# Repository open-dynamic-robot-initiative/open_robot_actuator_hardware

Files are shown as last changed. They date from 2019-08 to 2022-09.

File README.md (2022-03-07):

# Open Robot Actuator Hardware

**Click on the pictures below for more information**
## Electronics
| TI Evaluation Boards  | BLMC µDriver | Master Board |Details Wiring|
| ---  | --- |--- |---|
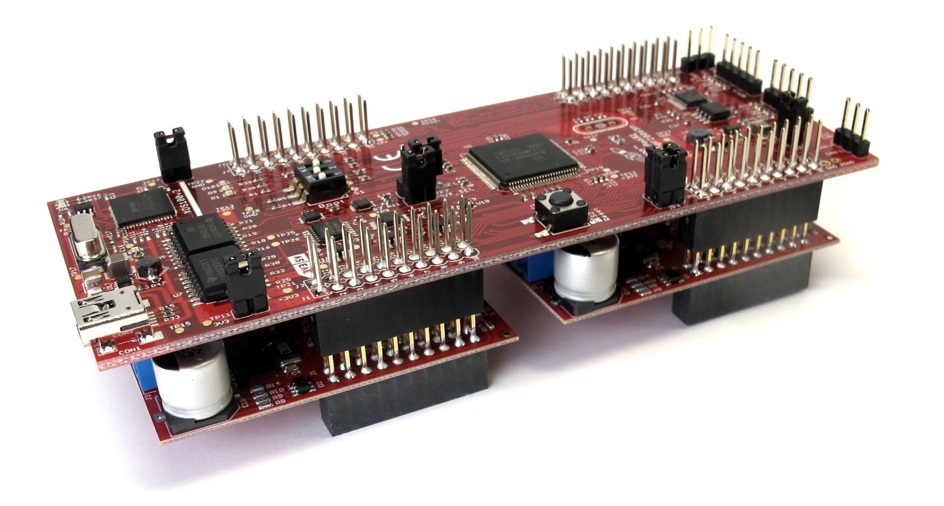
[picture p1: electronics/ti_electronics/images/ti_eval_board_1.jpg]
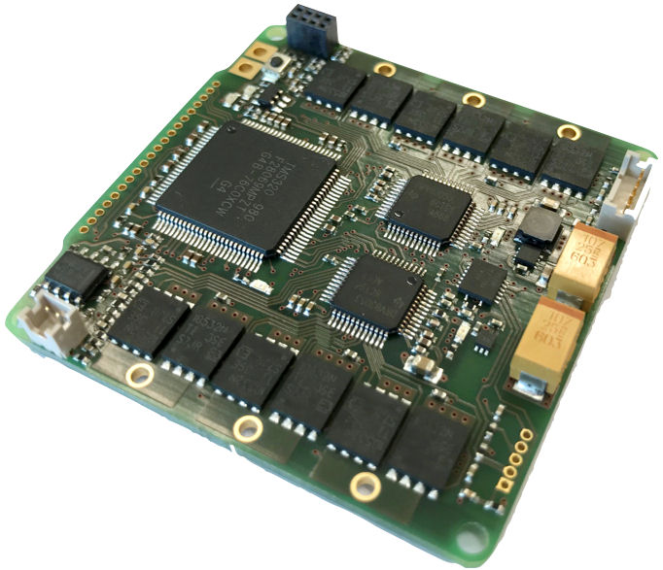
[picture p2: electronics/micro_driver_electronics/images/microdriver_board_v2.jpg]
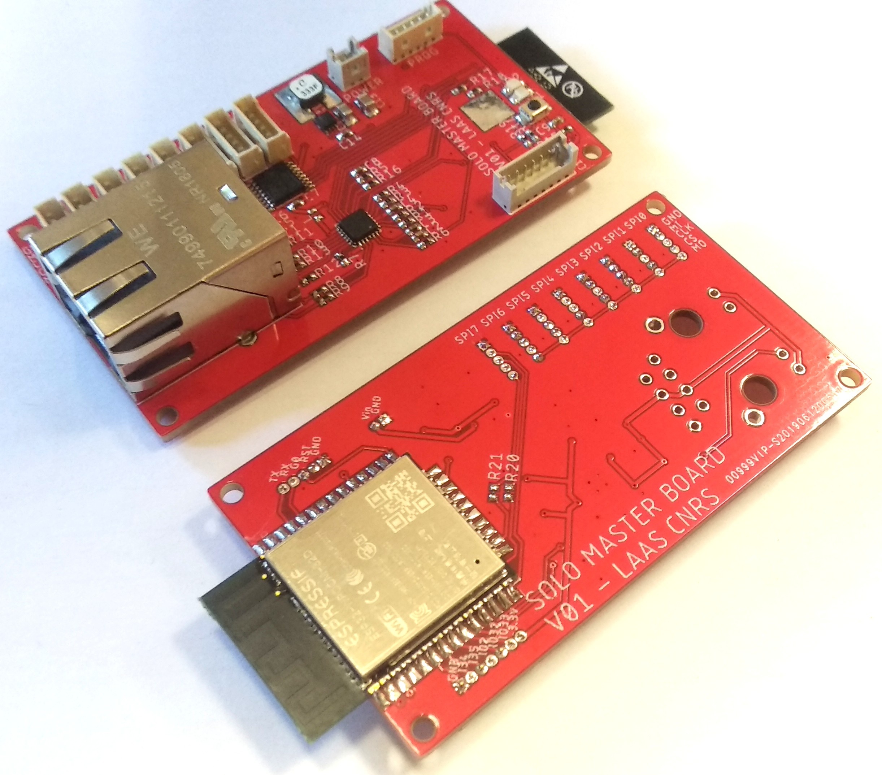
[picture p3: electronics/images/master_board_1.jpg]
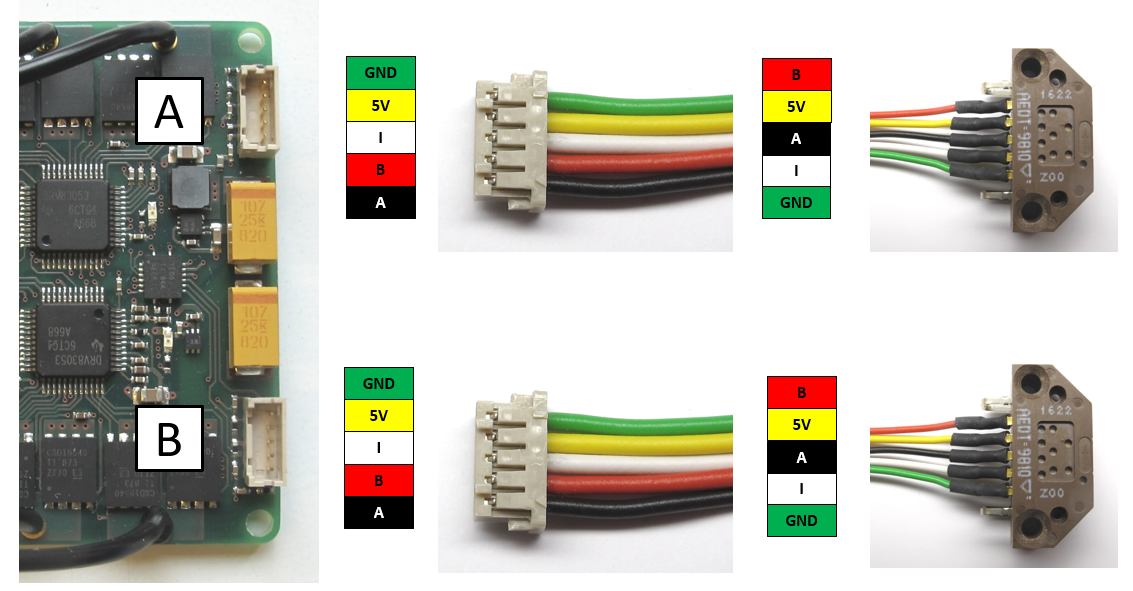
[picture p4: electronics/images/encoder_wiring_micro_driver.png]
| |   |   | |

## Mechanics
| Quadruped 8dof v2 (Solo8) | Quadruped 12dof (Solo12) | Biped 6dof (Bolt) | TriFingerEdu |
| --- | --- |--- |--- |
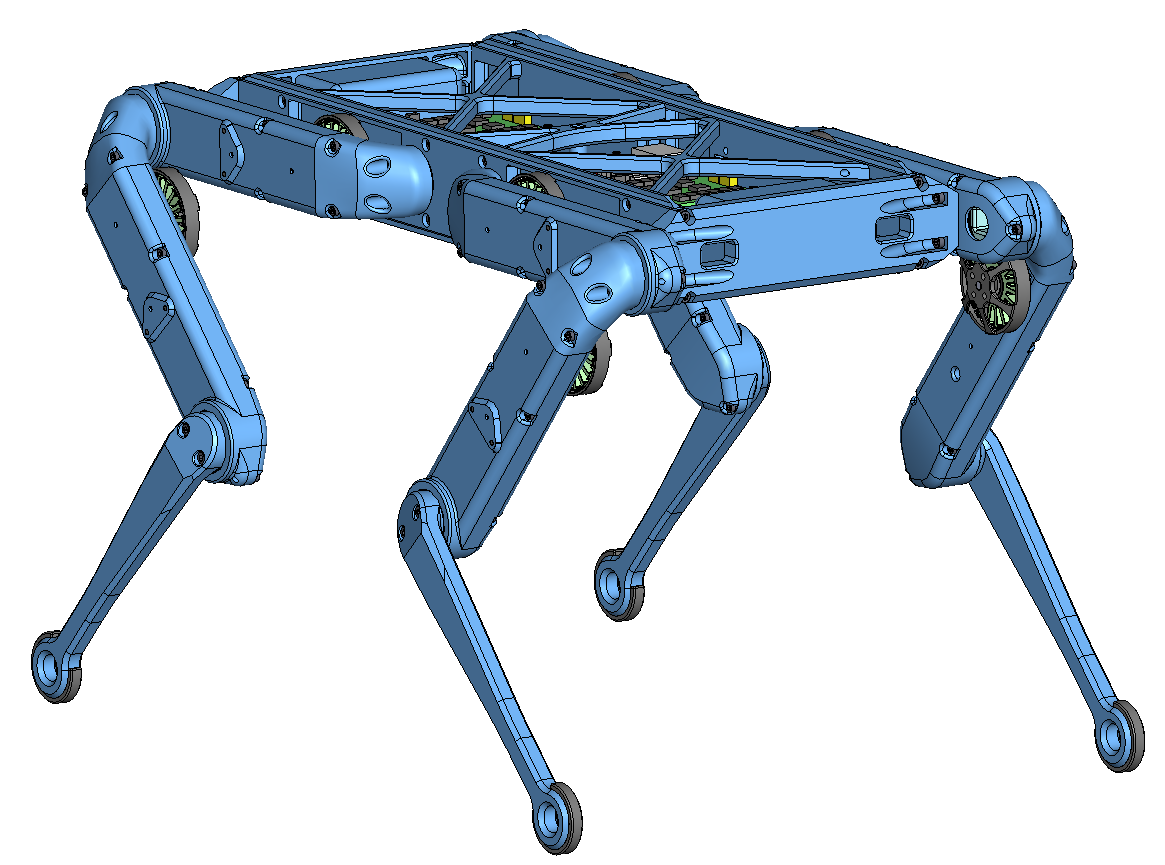
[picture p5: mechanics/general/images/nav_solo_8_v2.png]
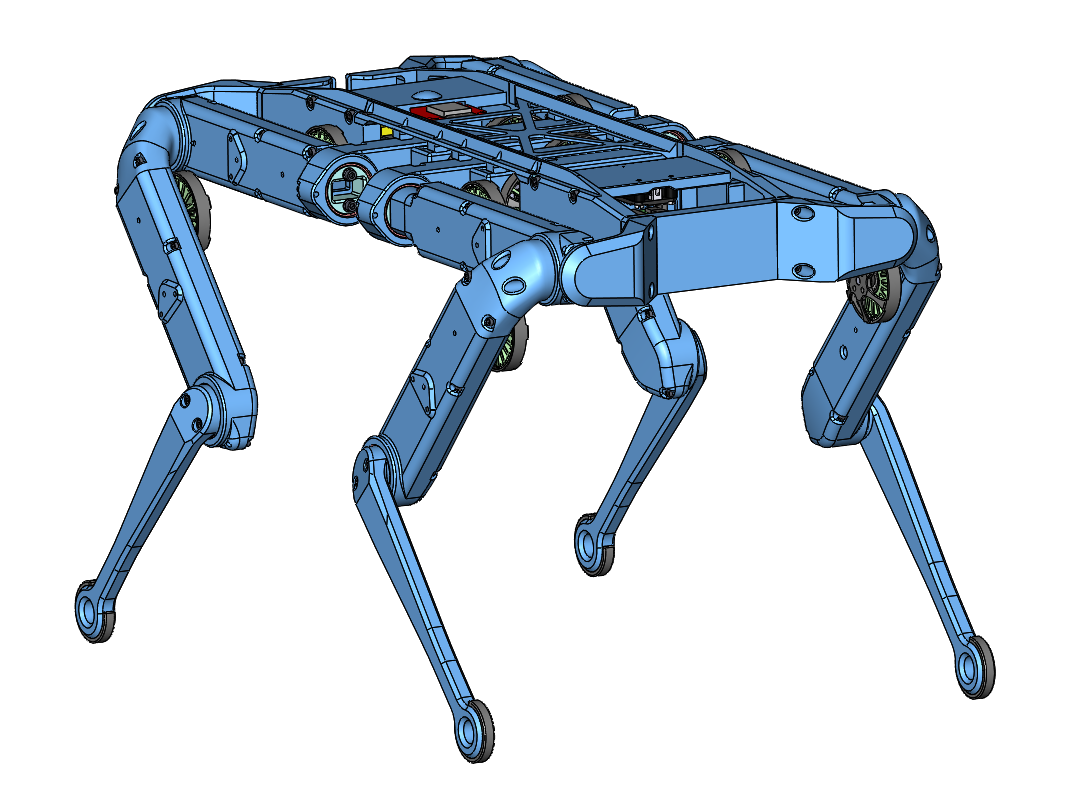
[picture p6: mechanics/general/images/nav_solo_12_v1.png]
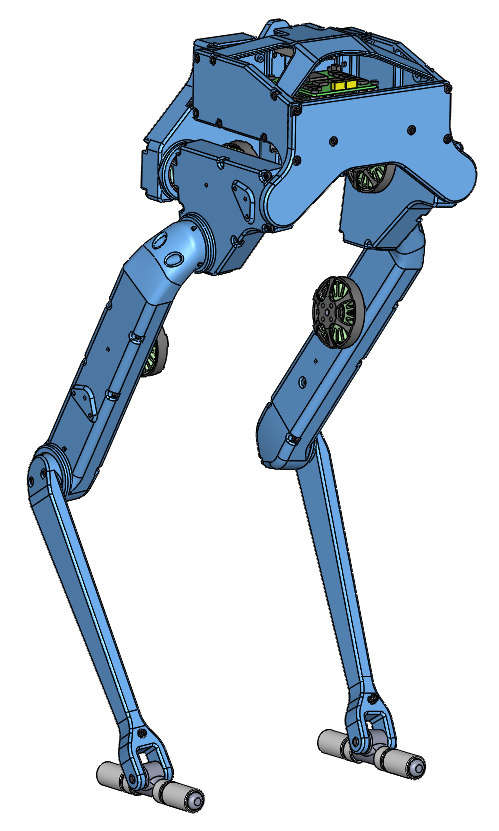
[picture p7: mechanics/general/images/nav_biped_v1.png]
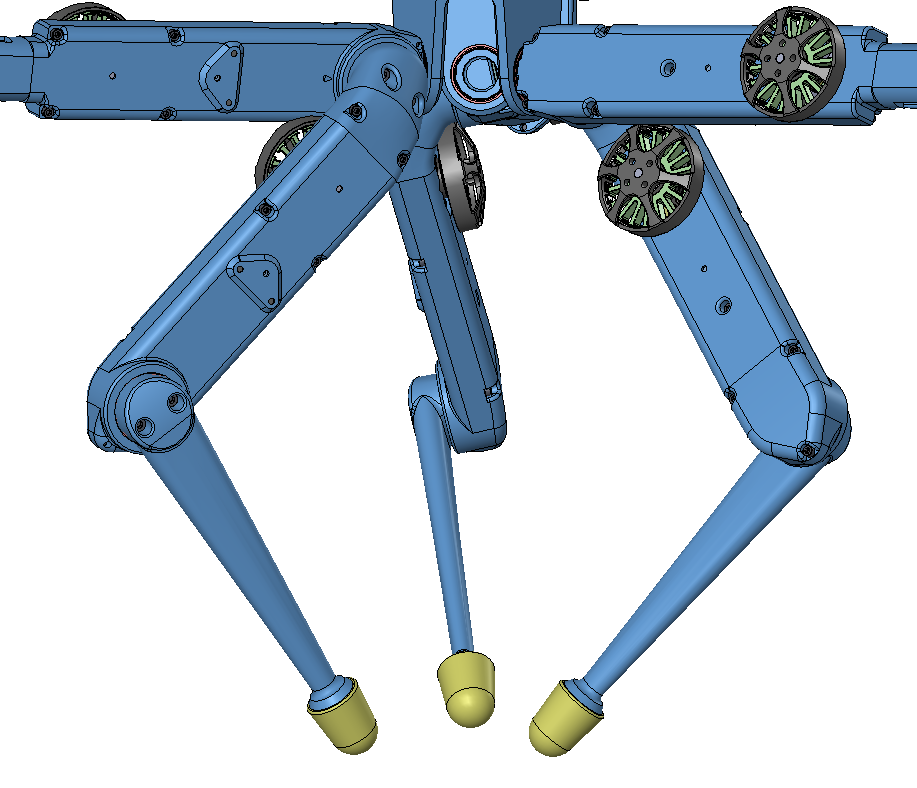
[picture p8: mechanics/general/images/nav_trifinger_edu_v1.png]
|||||

| 2dof Leg v2  | 3dof Leg | Biped Leg |FingerEdu |
| --- | --- |--- |--- |
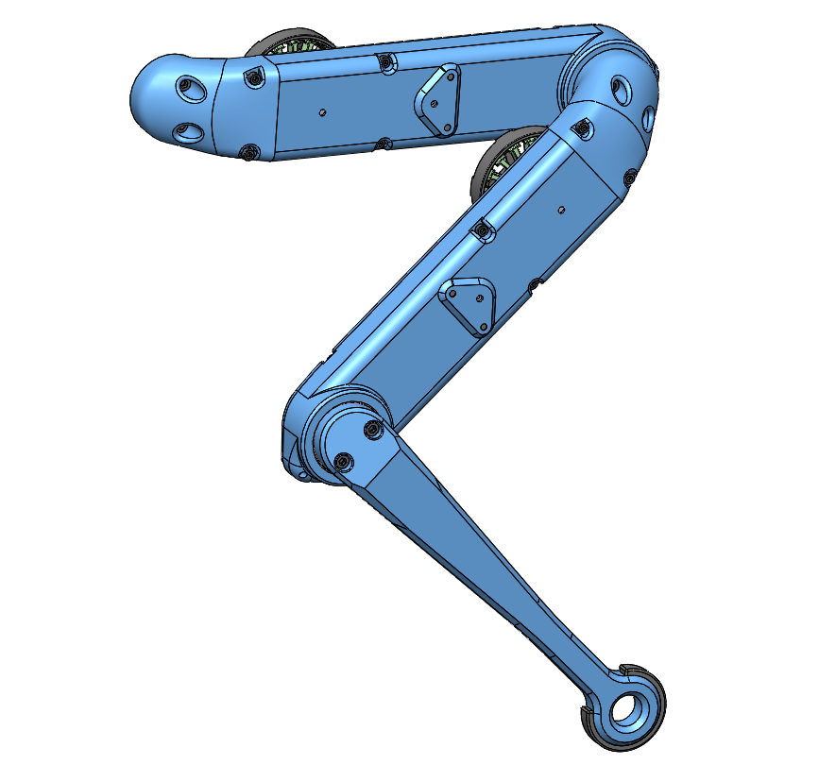
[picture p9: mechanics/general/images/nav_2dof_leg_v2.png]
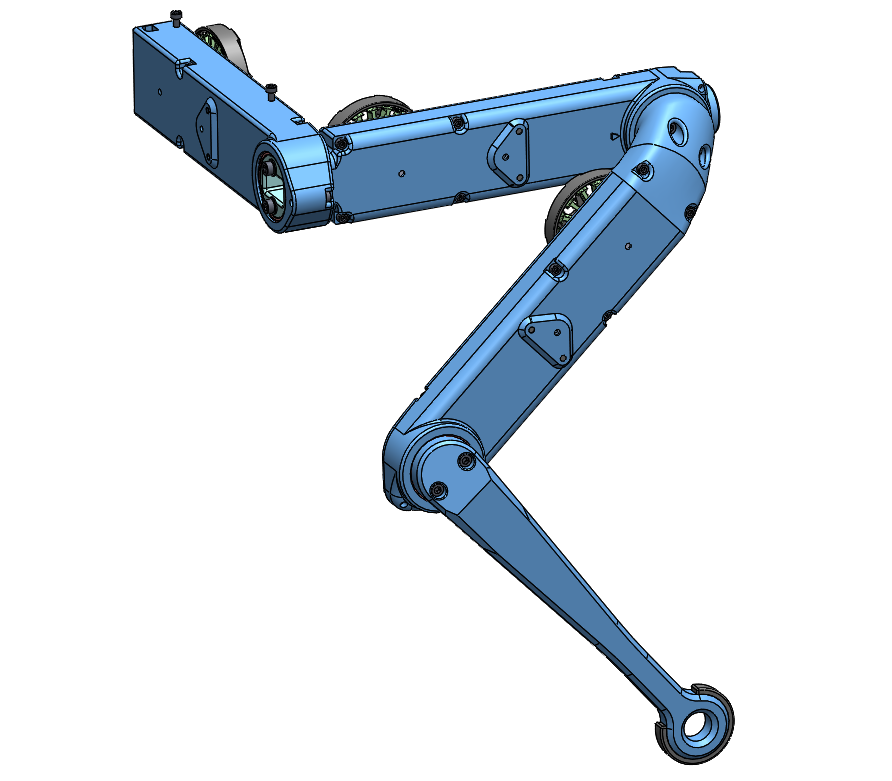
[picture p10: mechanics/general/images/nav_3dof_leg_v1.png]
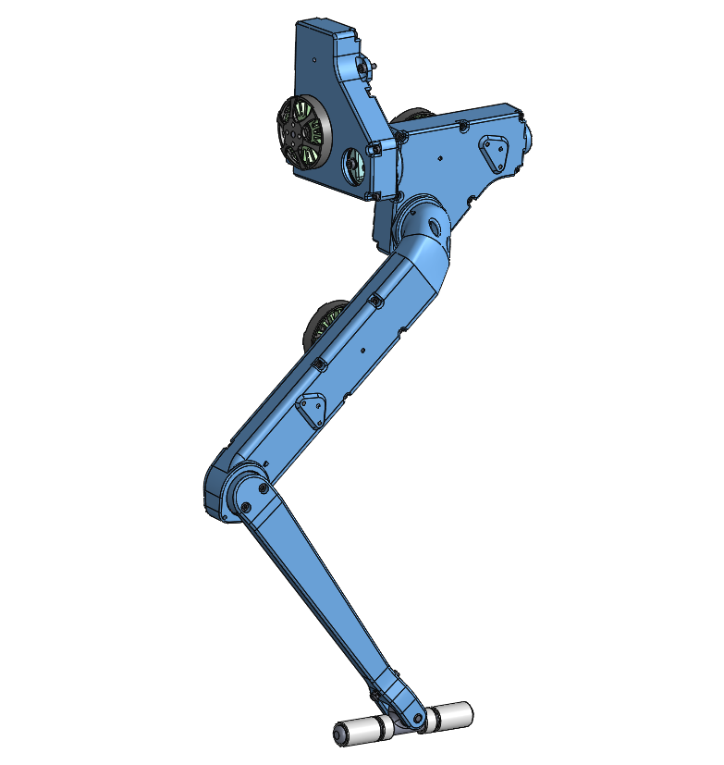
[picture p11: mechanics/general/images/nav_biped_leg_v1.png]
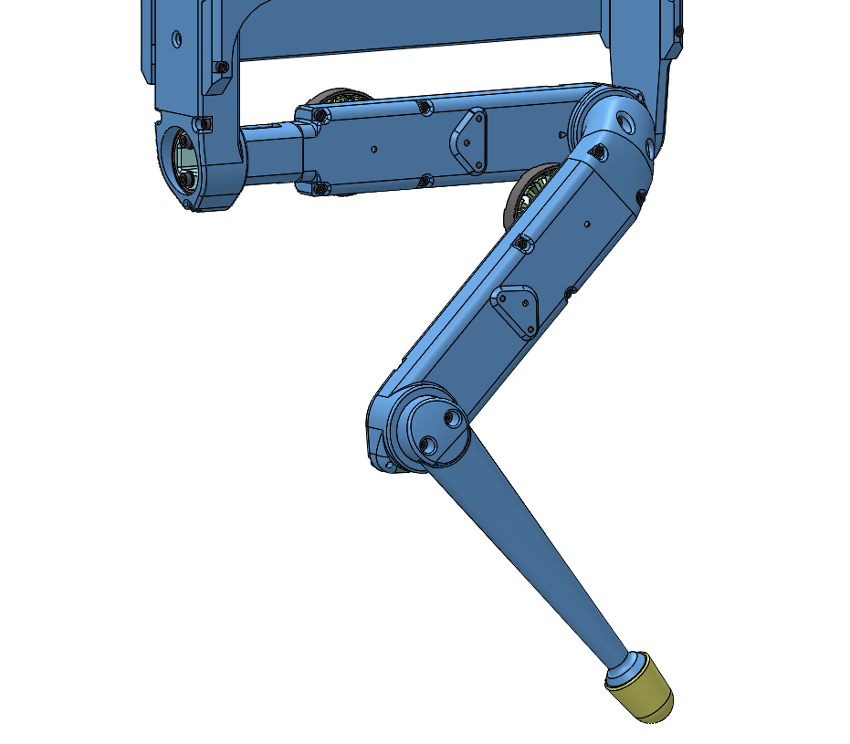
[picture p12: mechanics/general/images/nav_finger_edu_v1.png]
|   |   |   |  |

| Actuator Module Core v1| Actuator Module Core v1.1 | Details 3d Printed Parts | Details Machined Parts |
| ---  | --- |--- |--- |
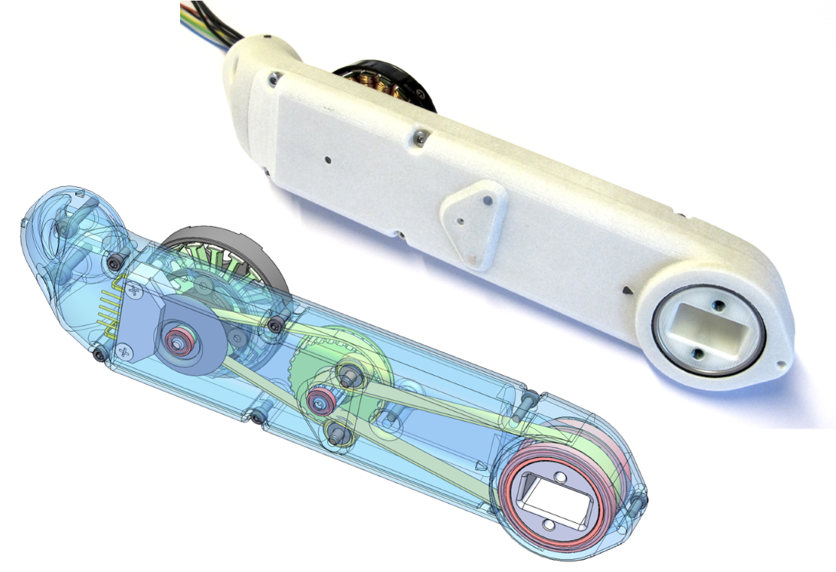
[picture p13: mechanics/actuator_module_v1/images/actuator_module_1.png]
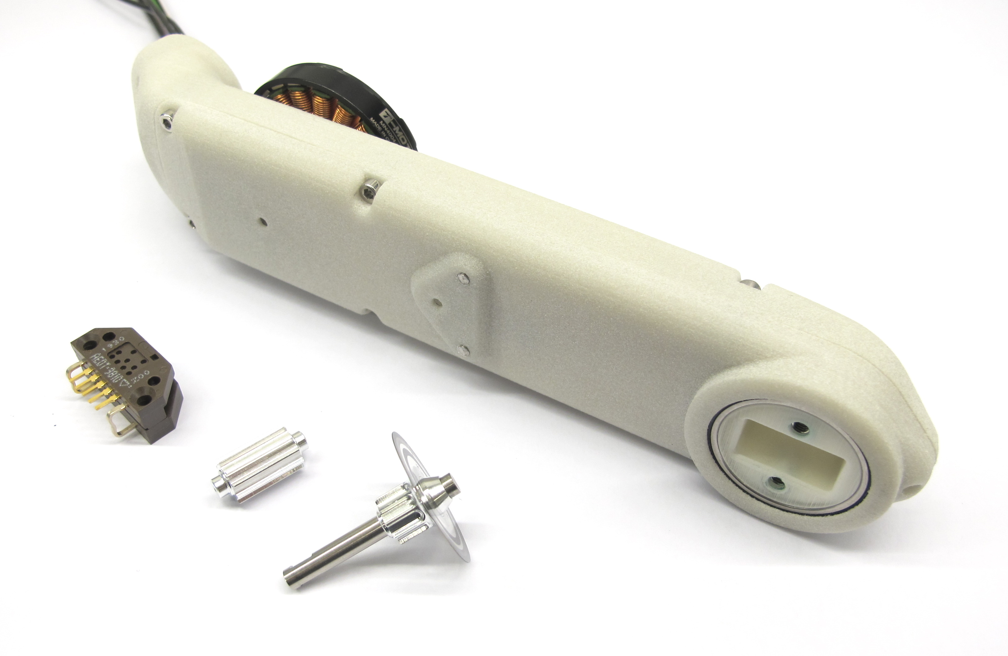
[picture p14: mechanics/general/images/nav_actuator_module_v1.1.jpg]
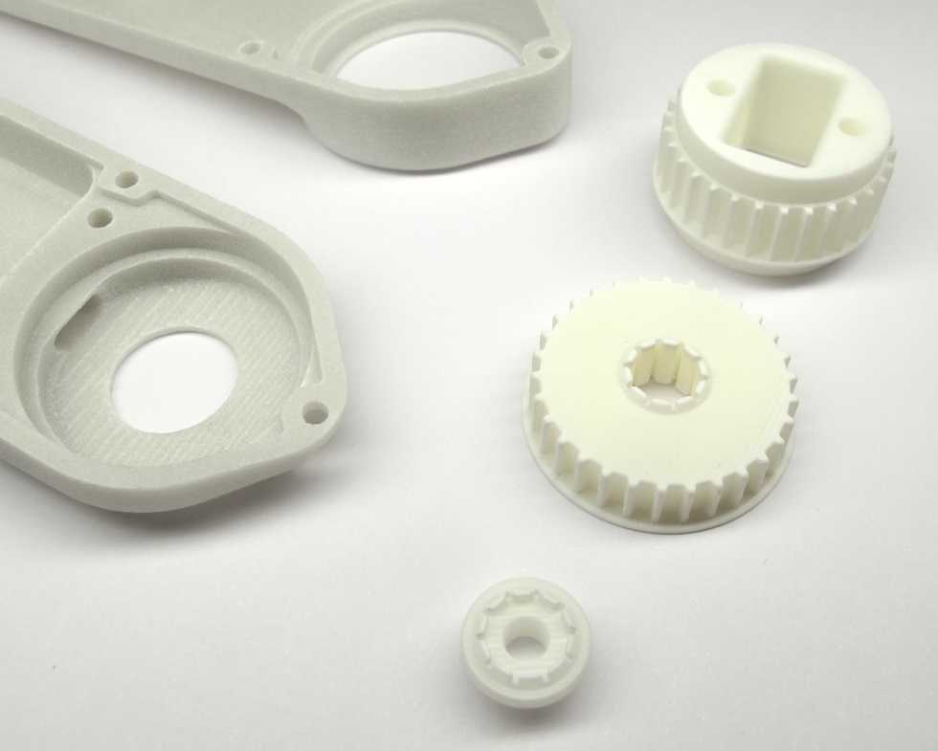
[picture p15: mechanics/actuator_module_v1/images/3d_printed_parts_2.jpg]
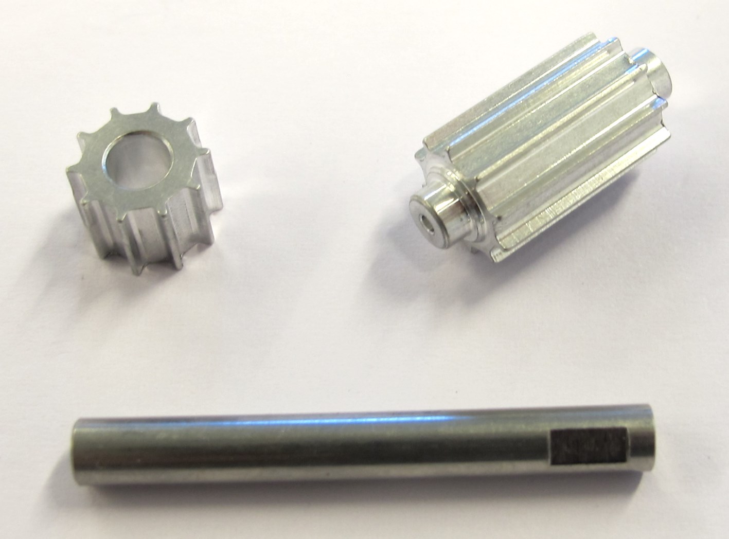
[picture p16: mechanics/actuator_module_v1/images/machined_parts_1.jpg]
| |  | |  |

| Quadruped 12dof v1.1<br>Autonomy Upgrade | Leg Test Stand v2 | NYU Finger | Dual Motor Testbed |
| ---  | --- |--- |---|
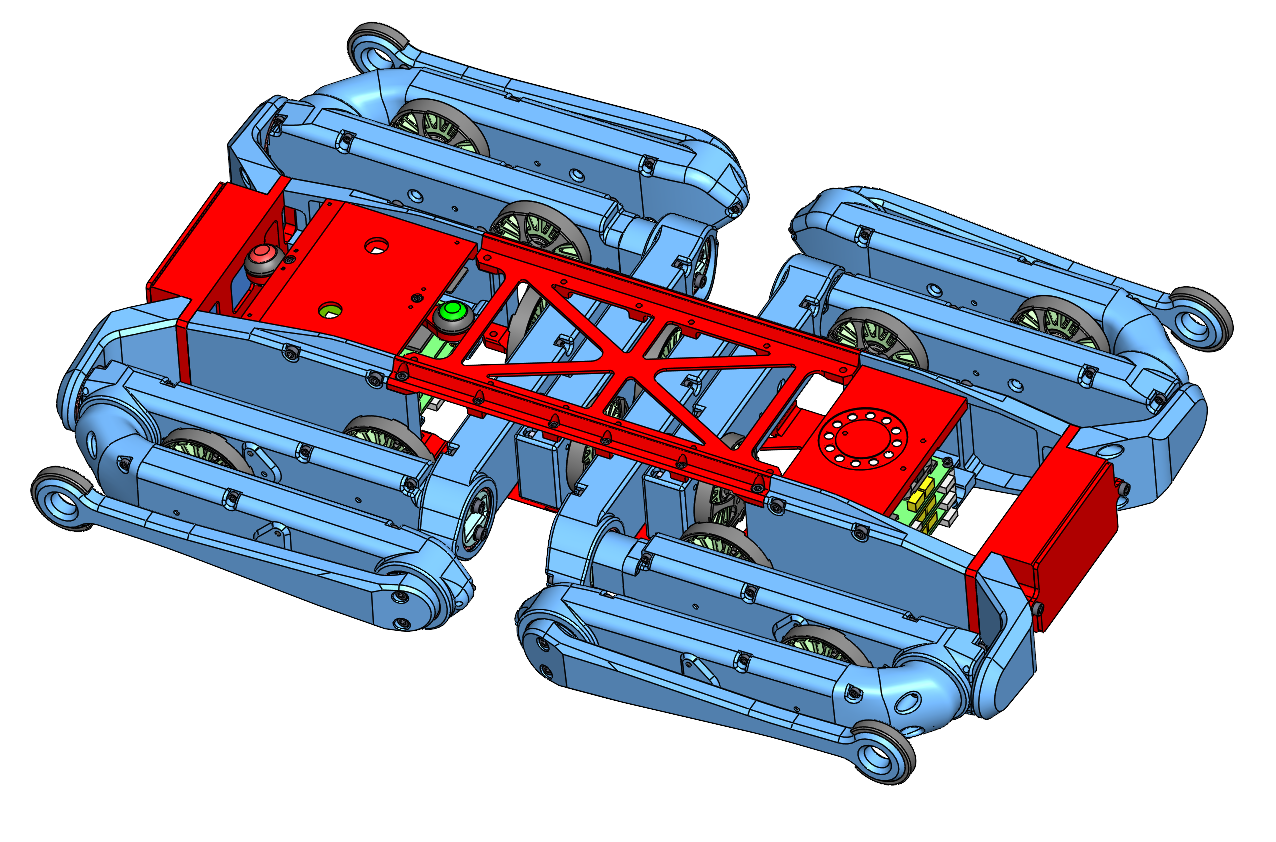
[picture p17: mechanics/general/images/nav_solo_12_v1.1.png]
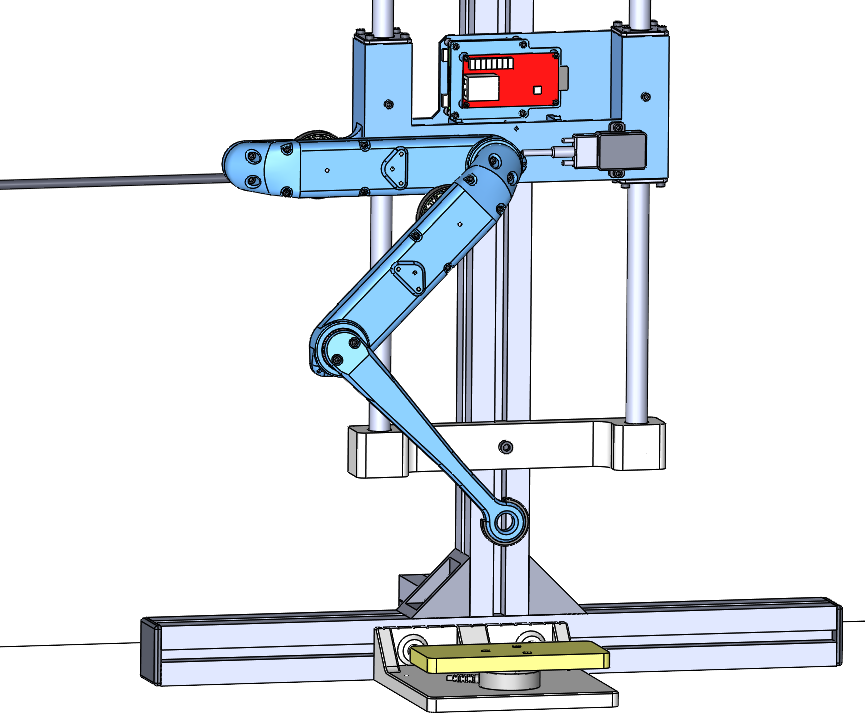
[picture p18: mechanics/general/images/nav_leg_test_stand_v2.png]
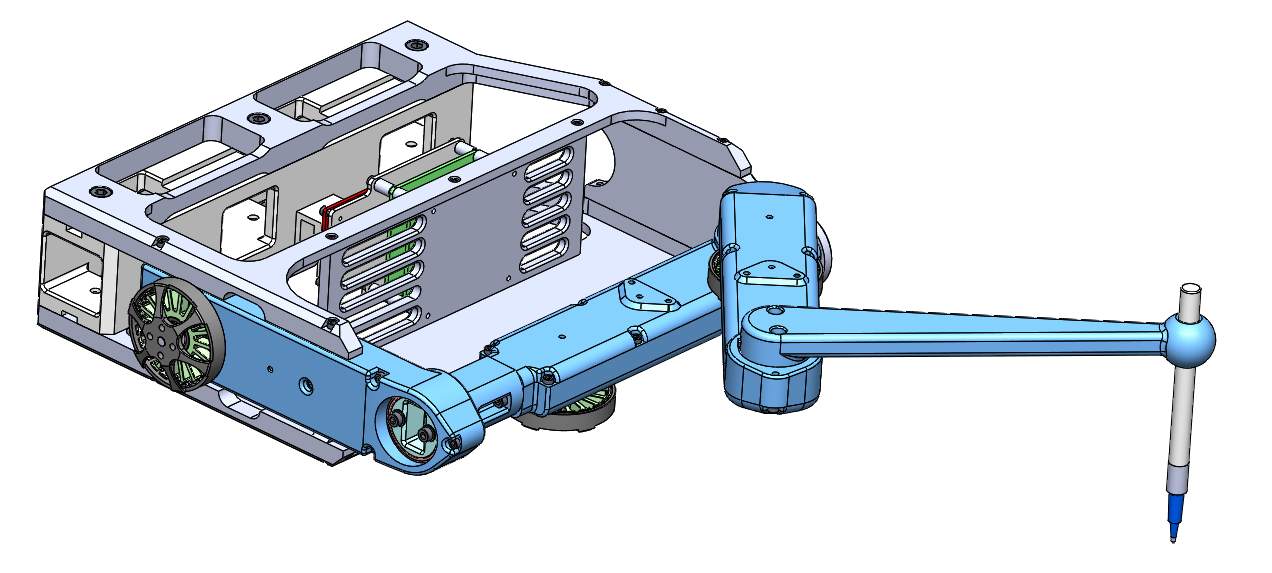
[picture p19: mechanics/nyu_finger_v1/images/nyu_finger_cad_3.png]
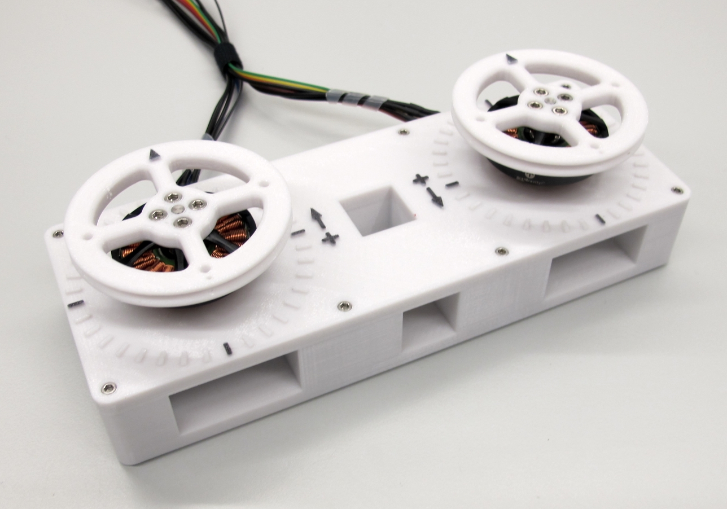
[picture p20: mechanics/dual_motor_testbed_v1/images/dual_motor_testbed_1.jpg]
| |  |  |  |

## More Details
| Mechanical Tools and Consumables |Electronic Components and Tools| Details Electronics<br>Quadruped Robot 12dof | Lower Legs |
| --- | --- | --- |--- |
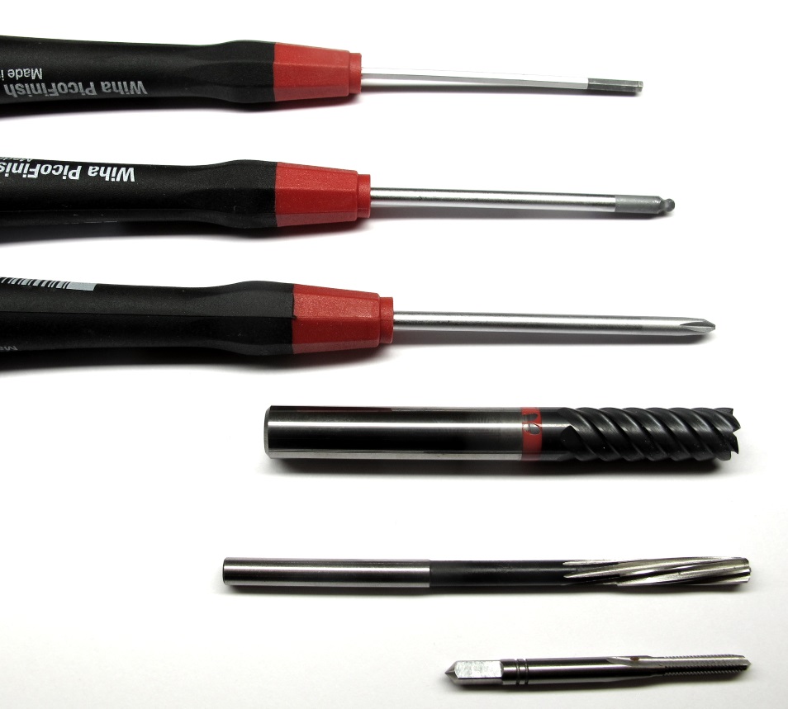
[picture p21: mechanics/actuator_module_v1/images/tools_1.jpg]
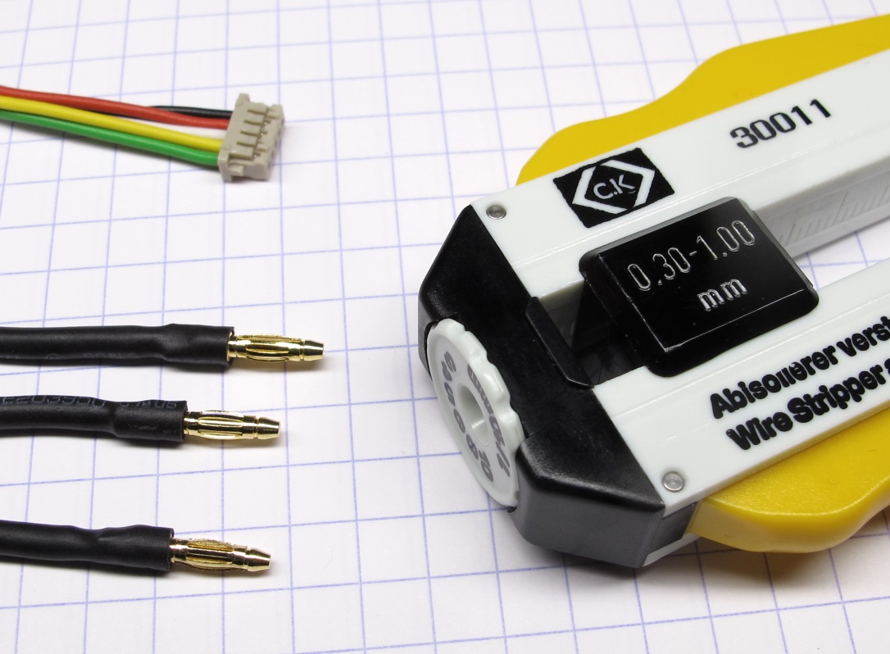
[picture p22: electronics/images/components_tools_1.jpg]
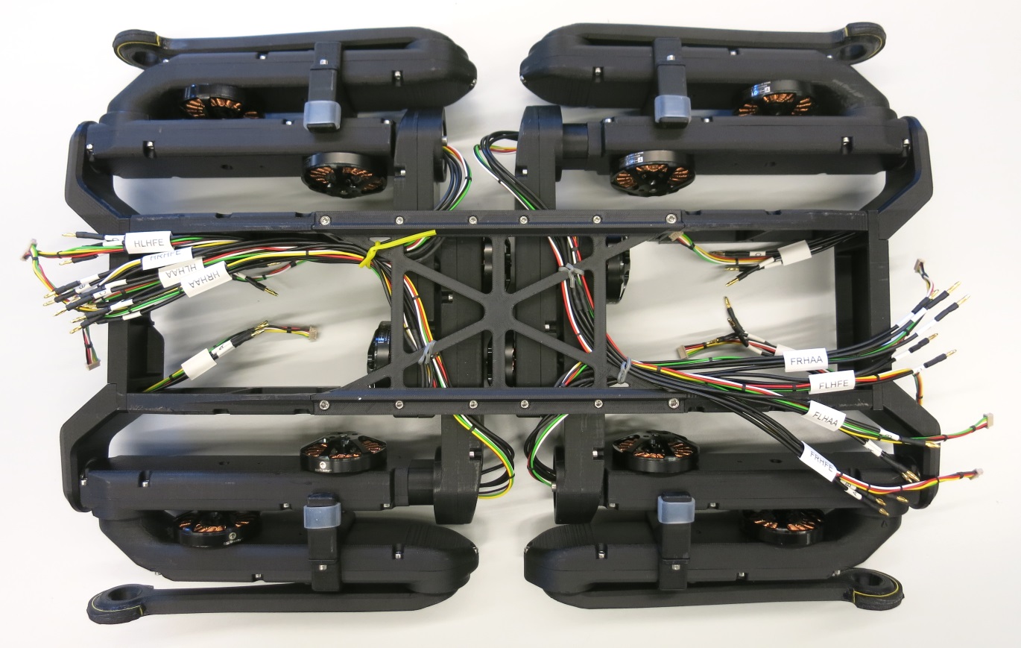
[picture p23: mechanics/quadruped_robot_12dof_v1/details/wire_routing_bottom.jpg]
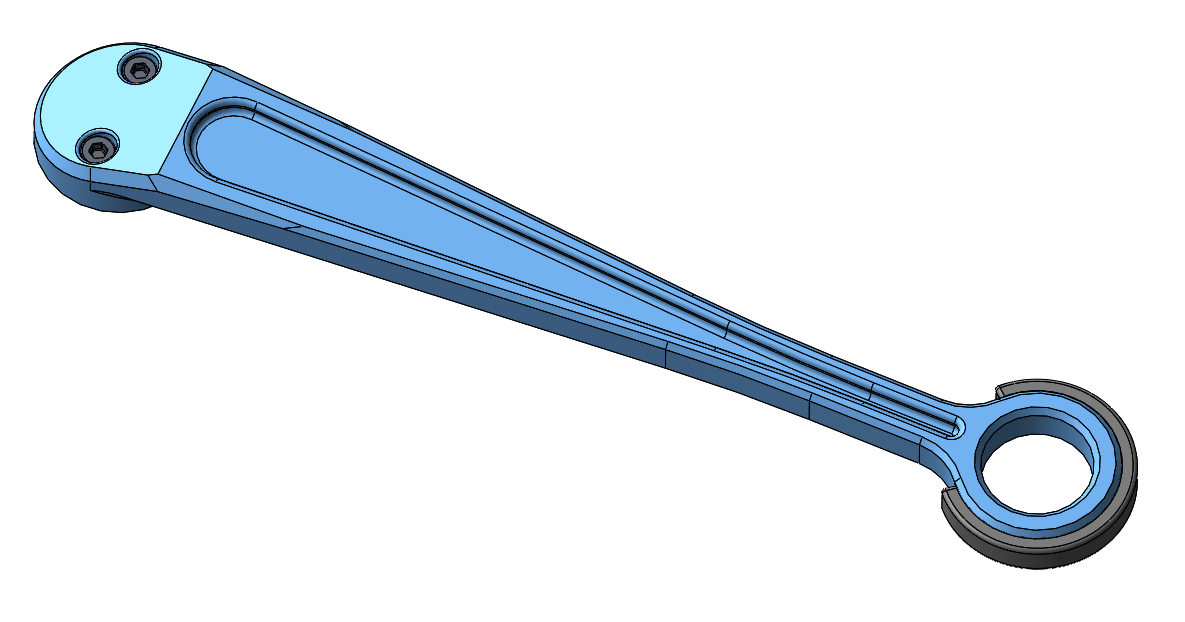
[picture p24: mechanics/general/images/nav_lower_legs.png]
|||  |   |

| Robot Calibration | Conventions | Known Issues |  |
| --- | --- | --- | --- |
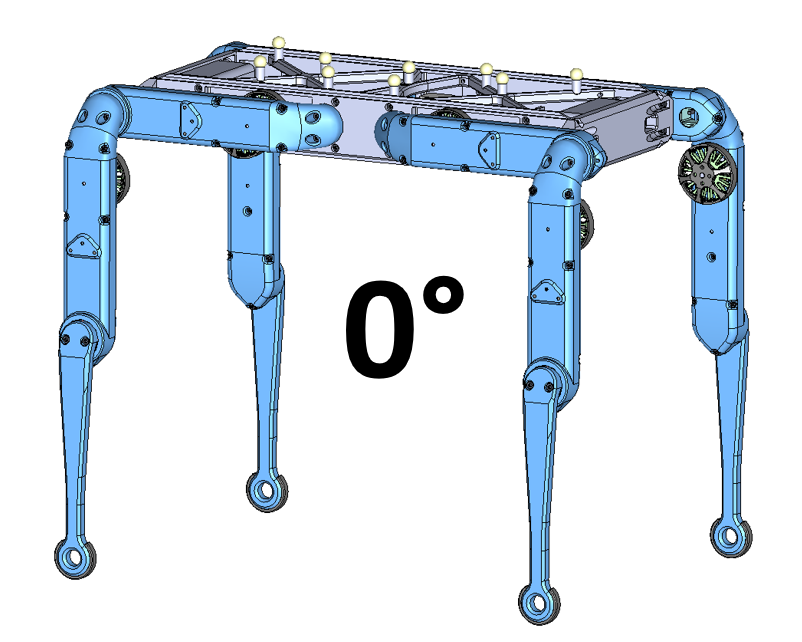
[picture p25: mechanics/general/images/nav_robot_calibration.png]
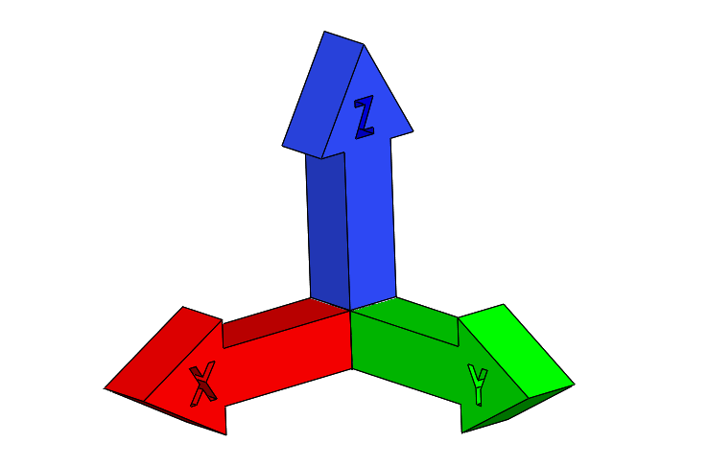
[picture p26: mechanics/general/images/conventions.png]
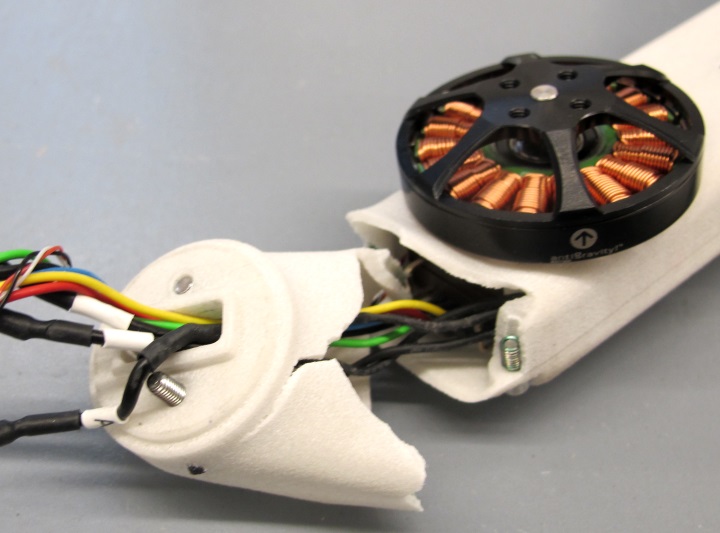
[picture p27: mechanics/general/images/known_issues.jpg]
|||||

## Step-by-Step Instructions
| Motor Preparation  | Motor Shaft Preparation | Encoder Preparation |Center Pulley Preparation|
| --- | --- | --- | --- |
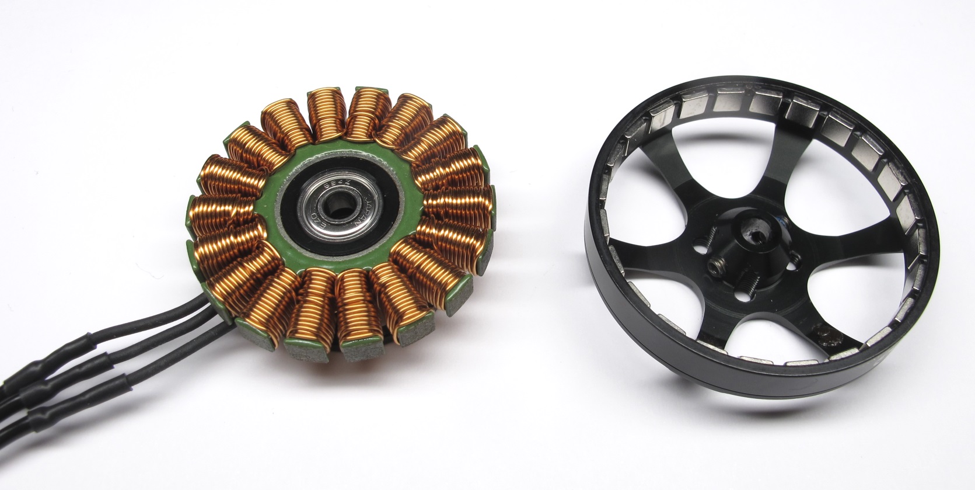
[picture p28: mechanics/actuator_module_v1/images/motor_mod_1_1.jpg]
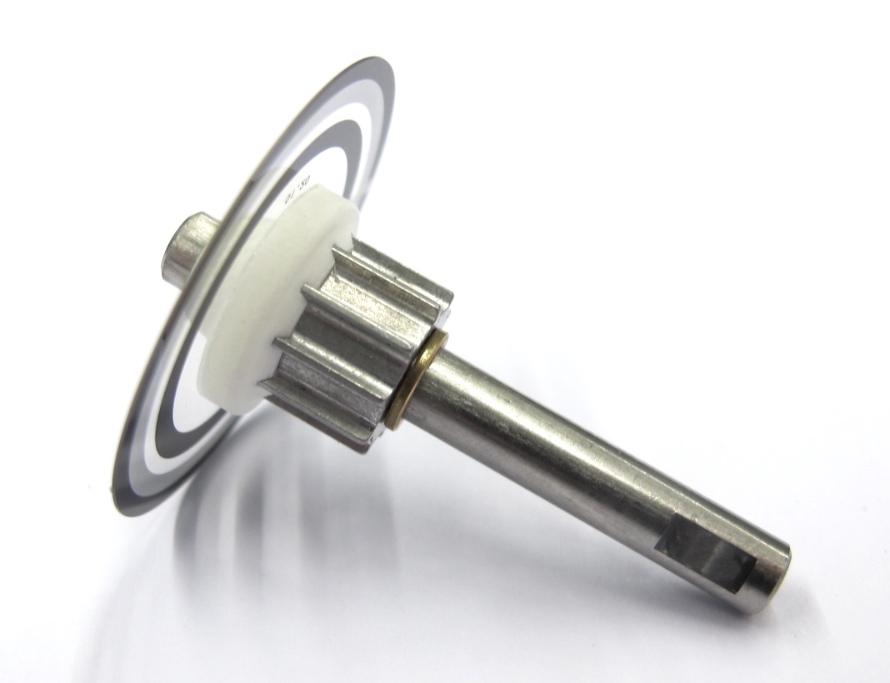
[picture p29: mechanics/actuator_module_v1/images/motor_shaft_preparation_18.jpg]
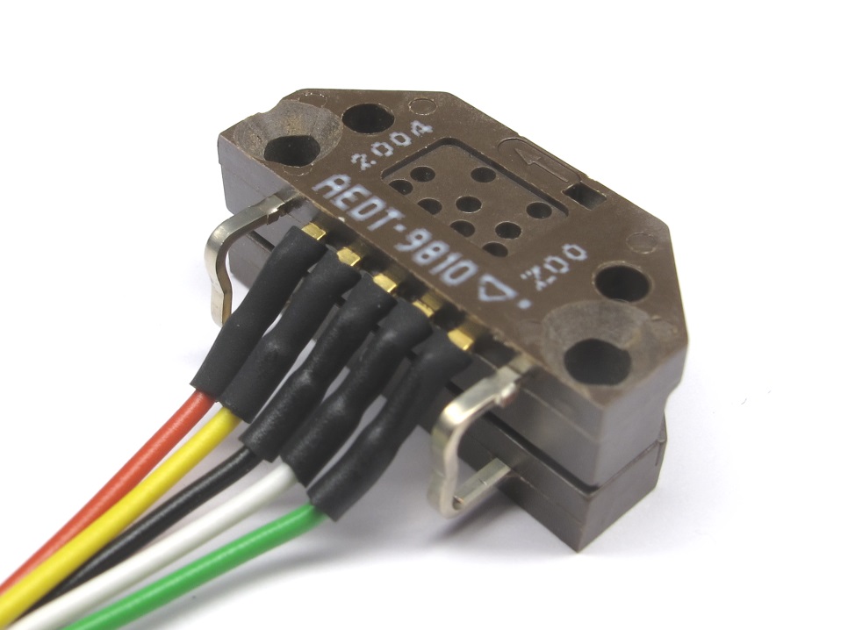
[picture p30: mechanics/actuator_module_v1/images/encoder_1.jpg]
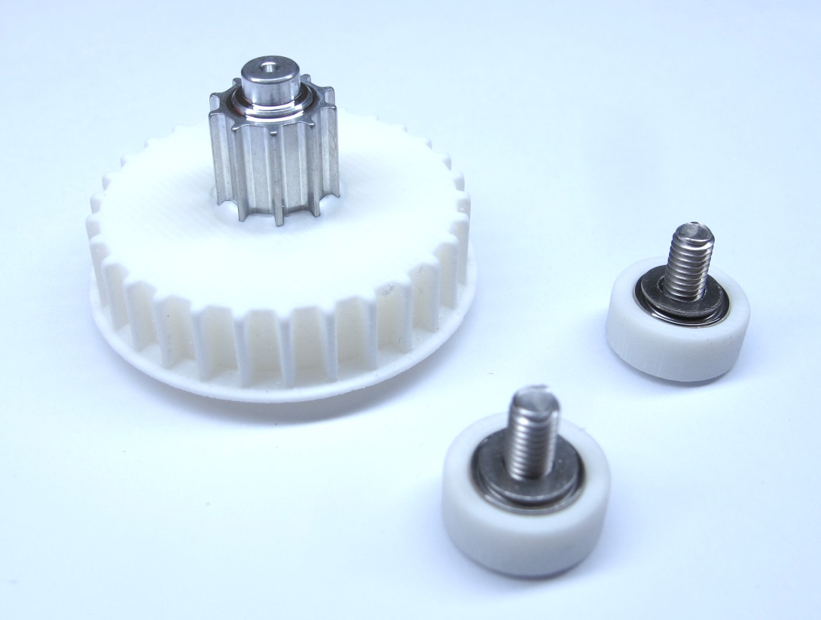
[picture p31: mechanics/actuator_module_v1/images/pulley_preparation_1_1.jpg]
| |   |   | |

| Output Pulley Preparation | Shell Preparation | Actuator Module Assembly |Actuator Module Testing|
| --- | --- | --- | --- |
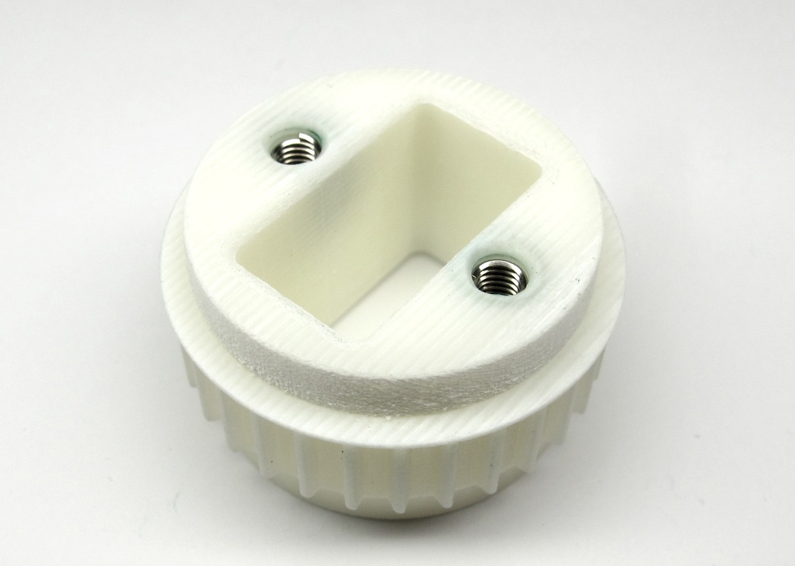
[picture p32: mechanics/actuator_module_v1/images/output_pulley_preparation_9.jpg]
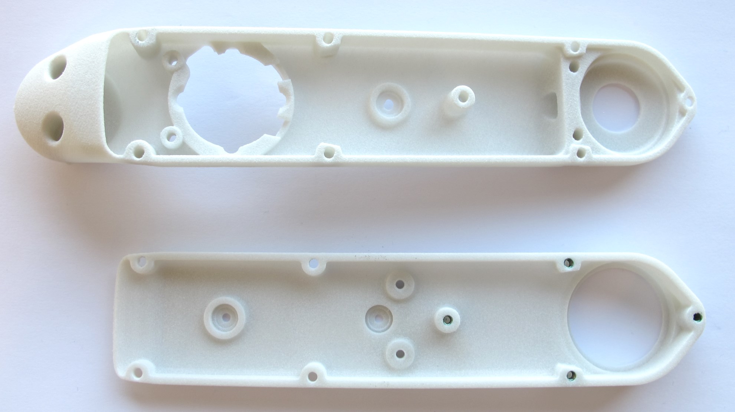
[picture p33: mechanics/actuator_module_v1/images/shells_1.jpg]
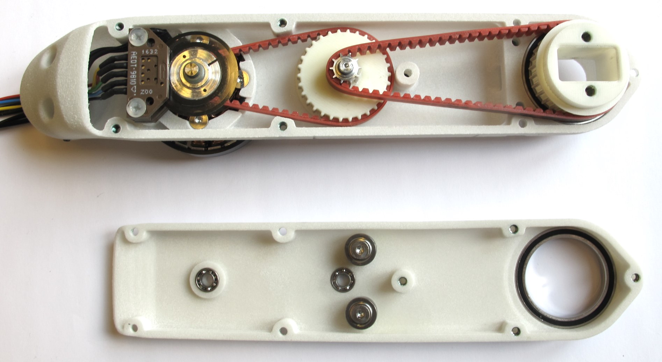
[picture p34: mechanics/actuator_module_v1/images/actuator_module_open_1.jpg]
| |   |   | |

## Old Versions for Reference
| Quadruped 8dof v1 | 2dof Leg v1 | Leg Test Stand v1| Foot Contact Switch |
| ---  | --- |--- |--- |
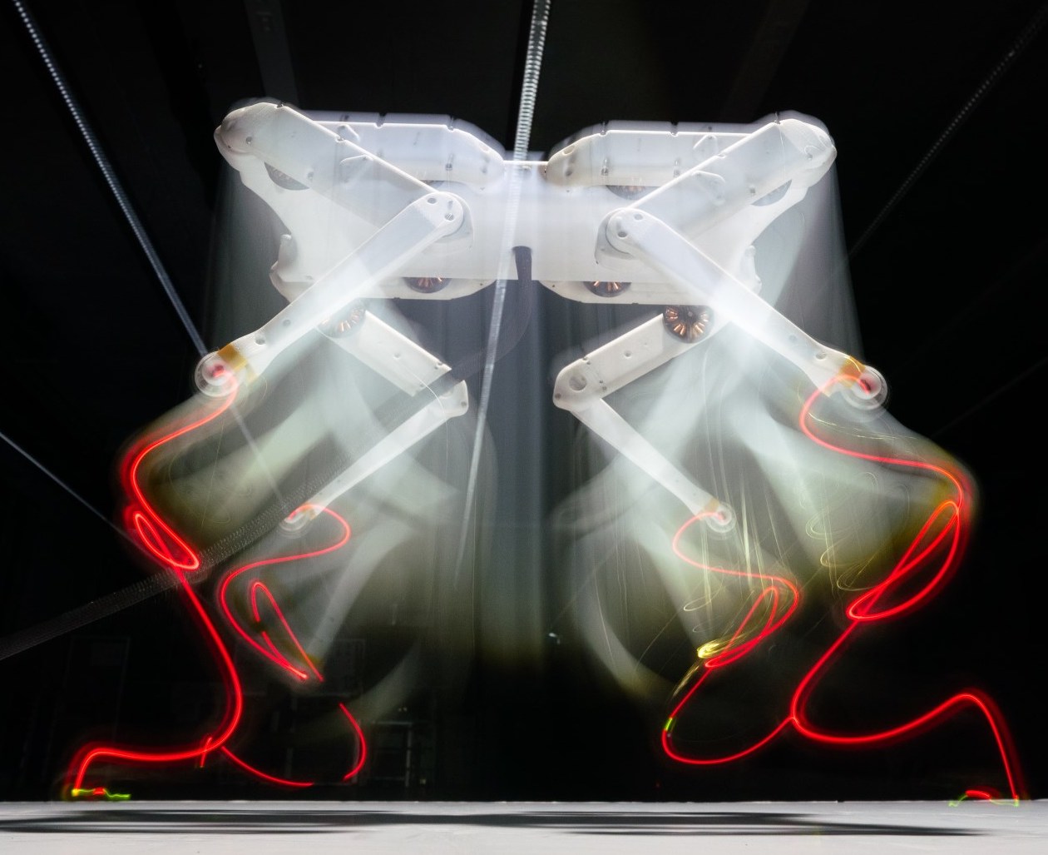
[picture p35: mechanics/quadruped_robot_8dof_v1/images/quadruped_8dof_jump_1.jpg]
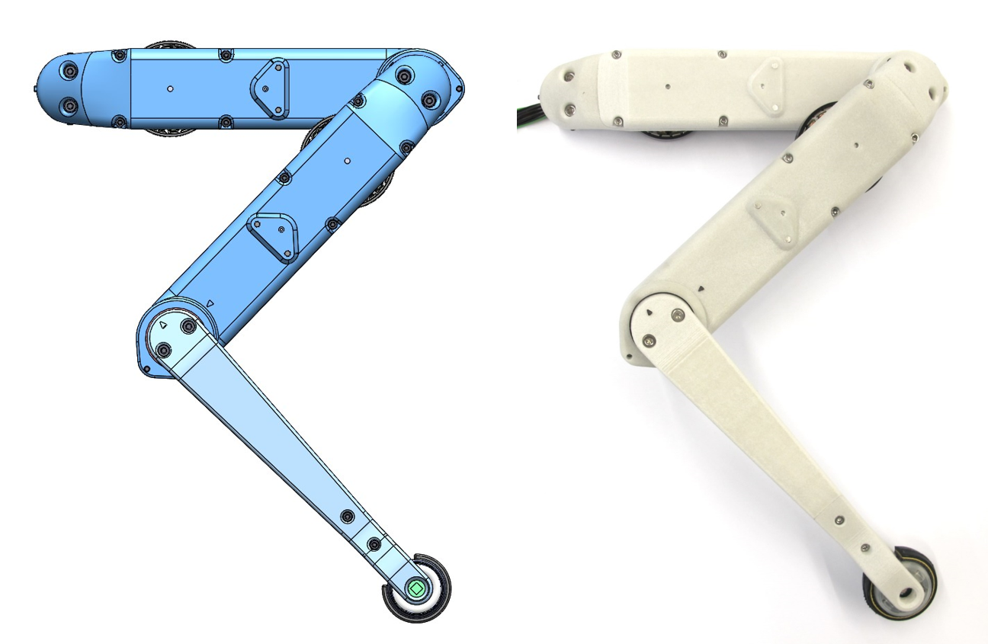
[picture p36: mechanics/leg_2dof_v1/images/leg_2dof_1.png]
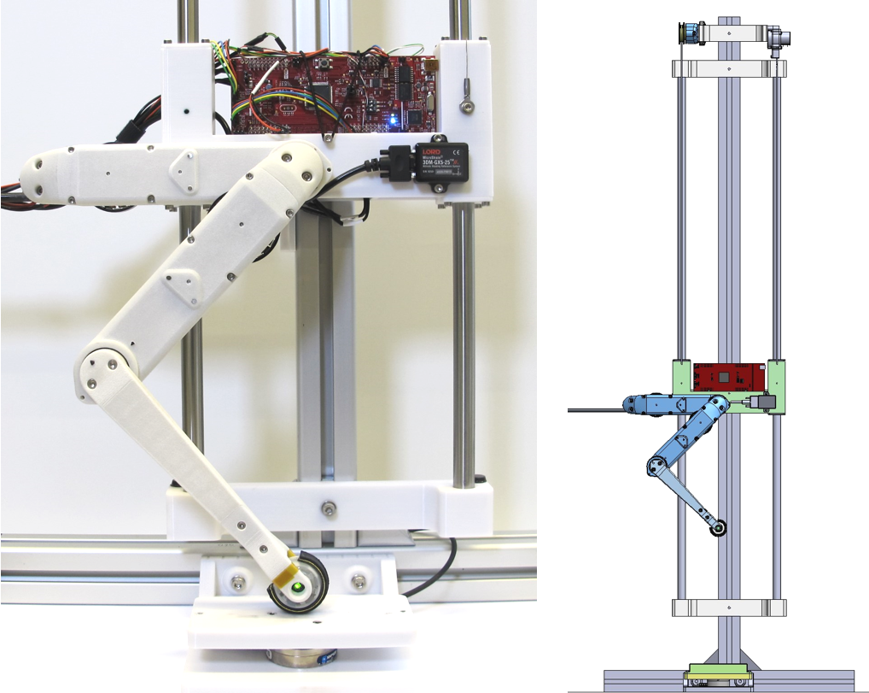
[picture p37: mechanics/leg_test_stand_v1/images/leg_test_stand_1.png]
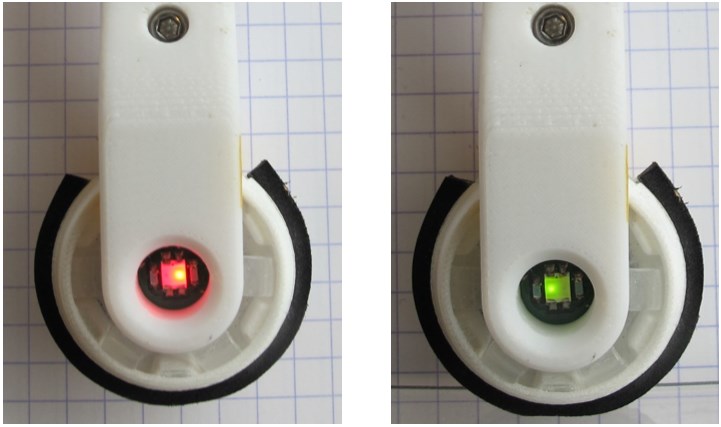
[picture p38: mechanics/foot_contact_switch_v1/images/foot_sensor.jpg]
| | |||

## More Information
[Open Dynamic Robot Initiative - Webpage](https://open-dynamic-robot-initiative.github.io)  
[Open Dynamic Robot Initiative - YouTube Channel](https://www.youtube.com/channel/UCx32JW2oIrax47Gjq8zNI-w)   
[Open Dynamic Robot Initiative - Forum](https://odri.discourse.group/categories)  
[Open Dynamic Robot Initiative - Paper](https://arxiv.org/pdf/1910.00093.pdf)  
[Hardware Overview](#open-robot-actuator-hardware)  
[Software Overview](https://github.com/open-dynamic-robot-initiative/open-dynamic-robot-initiative.github.io/wiki)  

## Authors
Jonathan Fiene  
Thomas Flayols  
Felix Grimminger  

## License
BSD 3-Clause License

## Copyright
Copyright (c) 2019-2021, Max Planck Gesellschaft and New York University

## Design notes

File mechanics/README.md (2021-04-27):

# Open Robot Actuator Mechanics

**Click on the pictures below for more information**

| Quadruped 8dof v2 | Quadruped 12dof | Biped 6dof | TriFingerEdu |
| ---  | --- |--- |--- |
|||||

| 2dof Leg v2  | 3dof Leg | Biped Leg |FingerEdu |
| --- | --- |--- |--- |
|   |   |   |  |

| Actuator Module Core v1| Actuator Module Core v1.1 | Details 3d Printed Parts | Details Machined Parts |
| ---  | --- |--- |--- |
| |  | |  |

| Quadruped 12dof v1.1<br>Autonomy Upgrade | Leg Test Stand v2 | NYU Finger | Dual Motor Testbed |
| ---  | --- |--- |---|
| |  |  |  |

## More Details
| Mechanical Tools and Consumables |Electronic Components and Tools| Details Electronics<br>Quadruped Robot 12dof | Lower Legs |
| --- | --- | --- |--- |
|||  |   |

| Robot Calibration | Conventions | Known Issues |  |
| --- | --- | --- | --- |
|||||

## Step-by-Step Instructions
| Motor Preparation  | Motor Shaft Preparation | Encoder Preparation |Center Pulley Preparation|
| --- | --- | --- | --- |
| |   |   | |

| Output Pulley Preparation | Shell Preparation | Actuator Module Assembly |Actuator Module Testing|
| --- | --- | --- | --- |
| |   |   | |

## Old Versions for Reference
| Quadruped 8dof v1 | 2dof Leg v1 | Leg Test Stand v1| Foot Contact Switch |
| ---  | --- |--- |--- |
| | |||

## More Information
[Open Dynamic Robot Initiative - Webpage](https://open-dynamic-robot-initiative.github.io)  
[Open Dynamic Robot Initiative - YouTube Channel](https://www.youtube.com/channel/UCx32JW2oIrax47Gjq8zNI-w)   
[Open Dynamic Robot Initiative - Forum](https://odri.discourse.group/categories)  
[Open Dynamic Robot Initiative - Paper](https://arxiv.org/pdf/1910.00093.pdf)  
[Hardware Overview](../README.md#open-robot-actuator-hardware)  
[Software Overview](https://github.com/open-dynamic-robot-initiative/open-dynamic-robot-initiative.github.io/wiki)  

## Authors
Jonathan Fiene  
Thomas Flayols  
Felix Grimminger  

## License
BSD 3-Clause License

## Copyright
Copyright (c) 2019-2021, Max Planck Gesellschaft and New York University

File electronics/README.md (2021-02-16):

# Open Robot Actuator Electronics

<br>**Click on the pictures below for more information**
## Electronics
| TI Evaluation Boards  | BLMC µDriver | Master Board |Details Wiring|
| ---  | --- |--- |---|
| |   |   | |

---
## More Information
[Open Dynamic Robot Initiative - Webpage](https://open-dynamic-robot-initiative.github.io)  
[Open Dynamic Robot Initiative - YouTube Channel](https://www.youtube.com/channel/UCx32JW2oIrax47Gjq8zNI-w)   
[Open Dynamic Robot Initiative - Forum](https://odri.discourse.group/categories)  
[Open Dynamic Robot Initiative - Paper](https://arxiv.org/pdf/1910.00093.pdf)  
[Hardware Overview](../#open-robot-actuator-hardware)  
[Software Overview](https://github.com/open-dynamic-robot-initiative/open-dynamic-robot-initiative.github.io/wiki)  

---
## Authors
Jonathan Fiene  
Thomas Flayols  
Felix Grimminger  

## License
BSD 3-Clause License

## Copyright
Copyright (c) 2019-2021, Max Planck Gesellschaft and New York University

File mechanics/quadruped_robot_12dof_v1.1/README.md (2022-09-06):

# Quadruped Robot 12dof v1.1
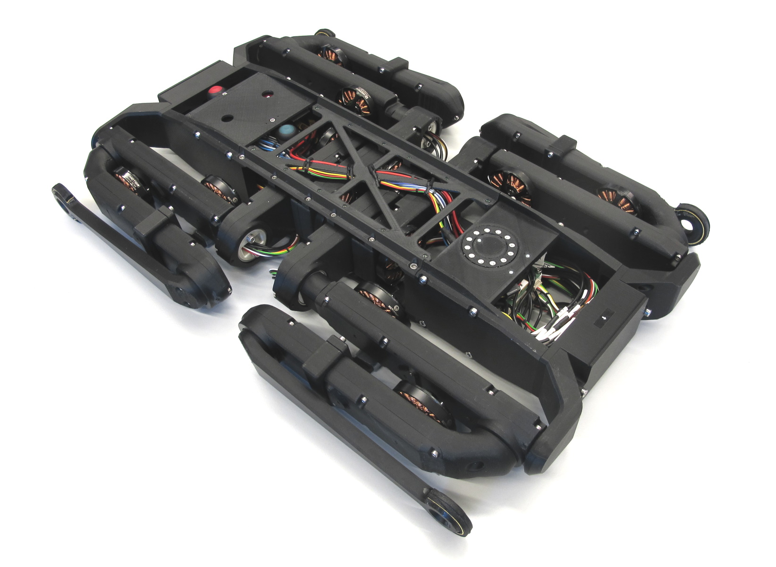
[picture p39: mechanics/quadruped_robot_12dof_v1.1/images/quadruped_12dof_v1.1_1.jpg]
<br>*Quadruped Robot 12dof v1.1 - Autonomy Upgrade - Weight: 2,8kg*<br>

## Description

* this page describes the autonomy upgrade for the [Quadruped 12dof v1 Robot](../quadruped_robot_12dof_v1/README.md#quadruped-robot-12dof-v1)
* onboard batteries and wireless communication will enable the robot to operate without power and ethernet wires
* using the onboard imu for state estimation will enable the robot to operate outside of the motion capture area
* the robot will carry two lithium polymer batteries - one battery pack in the front and one battery pack in the back of the robot
* the custom power management board will enable safe operation of the batteries, e-stop handling and real-time current and battery voltage measurements
* there is a status led ring with 12 RGB leds on the top of the robot
* there are two payload interfaces with mounting holes to attach additional components to the top or the bottom of the robot
* the estimated weight increase for this upgrade is about 300g
* the components that were upgraded are marked red in the screenshot below

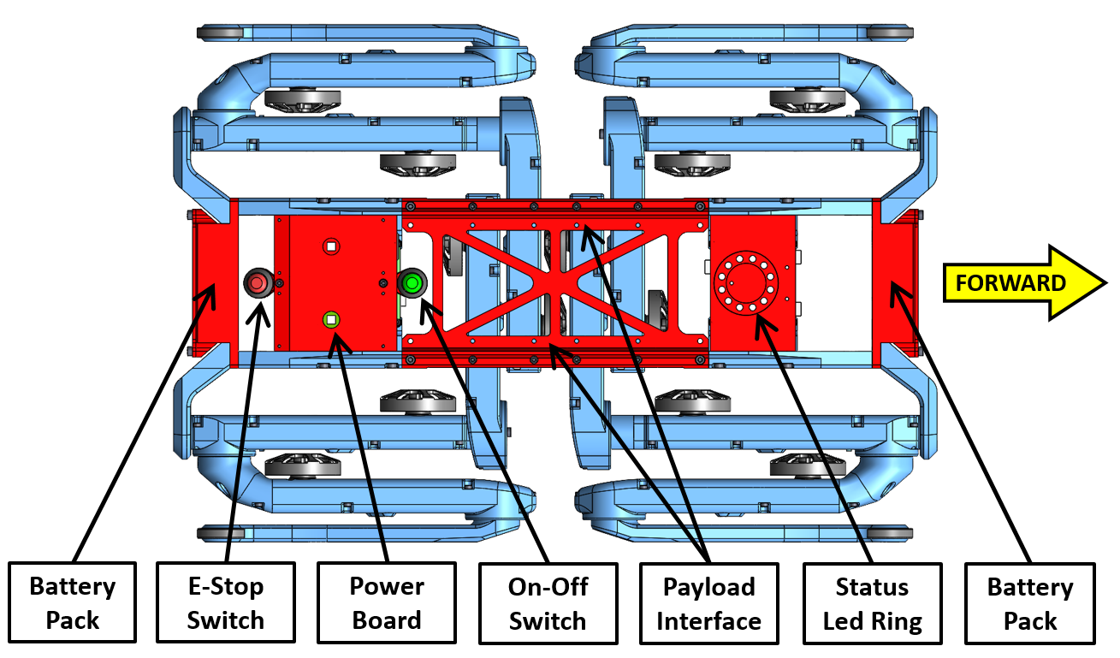
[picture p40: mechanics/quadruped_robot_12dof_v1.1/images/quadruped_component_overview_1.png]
<br>*Quadruped 12dof v1.1 Overview - the updated components are marked in red.* <br>

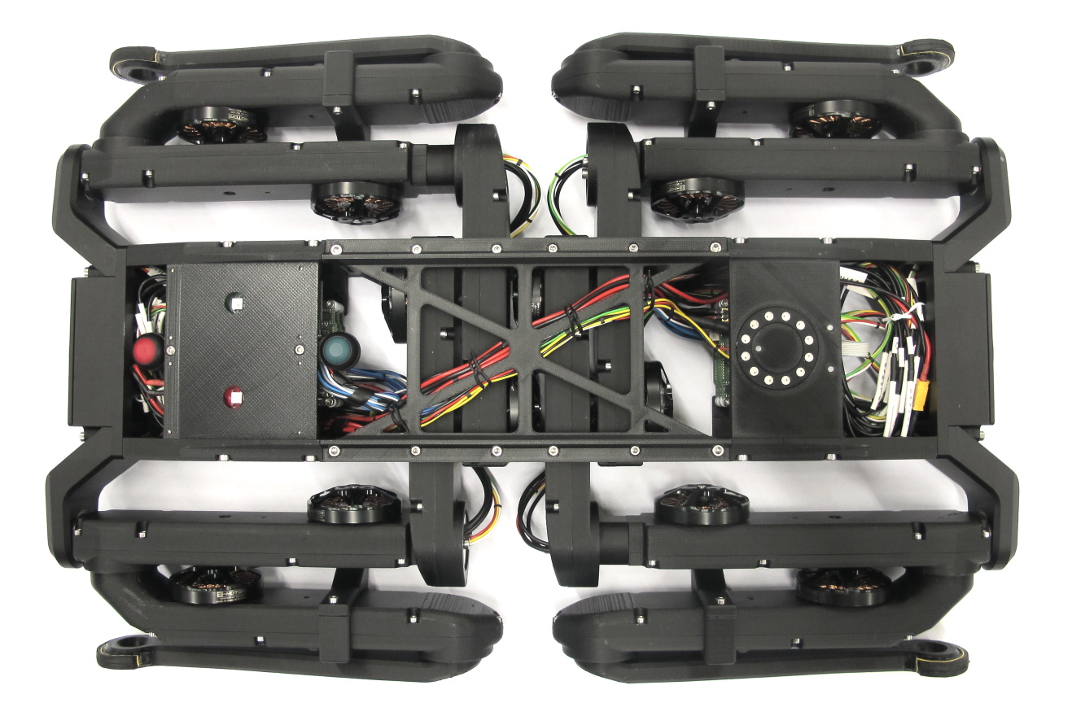
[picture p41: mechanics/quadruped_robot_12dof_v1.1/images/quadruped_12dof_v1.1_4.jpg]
<br>*Quadruped Robot 12dof v1.1 - Top View*<br>

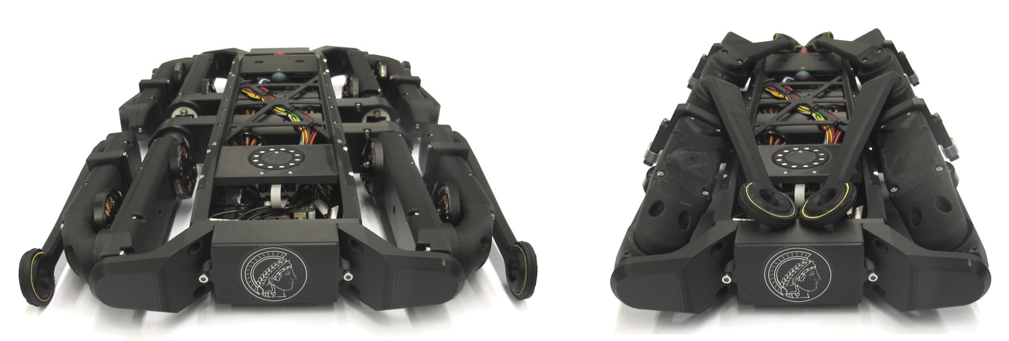
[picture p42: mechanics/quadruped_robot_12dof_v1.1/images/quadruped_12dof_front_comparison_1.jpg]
<br>*Quadruped Robot 12dof v1.1 - Front View<br>Sitting - dimensions: 46cm x 31cm x 6cm<br>Folded - dimensions: 46cm x 22cm x 9cm*<br>

---
## Electronics

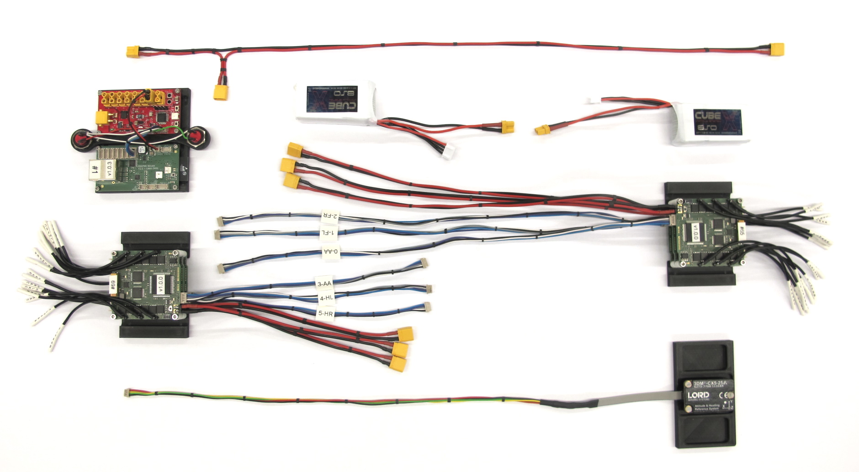
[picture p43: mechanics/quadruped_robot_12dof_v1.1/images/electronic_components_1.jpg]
<br>*Electronic Components Overview - weight: 463g*<br>  

### Power Management Board

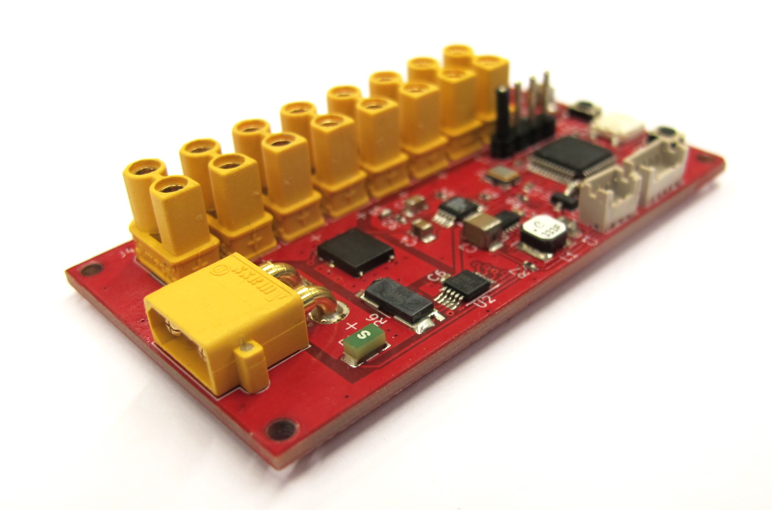
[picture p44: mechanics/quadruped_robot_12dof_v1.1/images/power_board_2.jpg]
<br>*Power Management Board - weight: 16g*<br>  

* this custom Power Management Board is being developed by [Thomas Flayols](https://github.com/thomasfla)
* Documentation: [Power Board GitHub Page](https://github.com/open-dynamic-robot-initiative/power-board)
* monitors battery voltage and current
* reads on/off switch and e-stop
* cuts battery power if the e-stop is activated
*	inrush current limitation
*	SPI interface for communication with the Master Board
*	8 x XT30 output connectors
* dimensions: 65mm x 35mm
* mounting holes: ø 2,1mm / spacing 61mm x 31mm
* weight: 16g

## Off-the-shelf Components

### Lithium Polymer Batteries
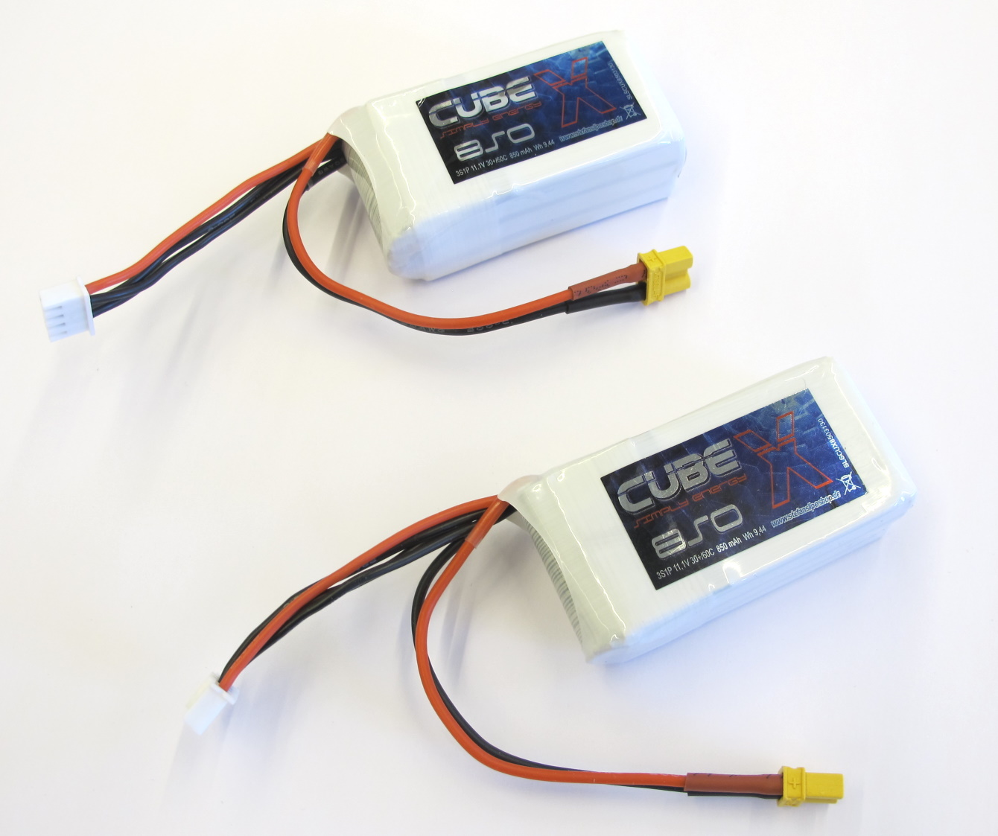
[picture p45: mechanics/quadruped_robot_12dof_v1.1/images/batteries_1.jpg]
<br>*Lithium Polymer Batteries - weight: 68g each*<br>  

* SLS X-Cube 850mAh lithium polymer batteries
* 3S1P / 11,1V / 30C continous / 60C burst
* weight: 68g
* dimensions: 60mm x 30mm x 21mm
* power connector: XT 30
* balancer connector: XH
* don't use the lipo batteries without a power management board!
* Ordering information [below](#bill-of-materials---upgrade-quadruped-robot-12dof-v11)

### Switches
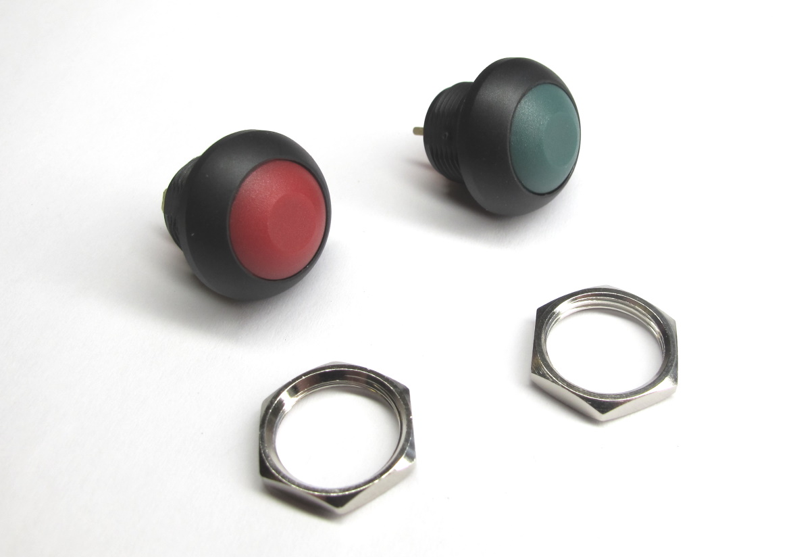
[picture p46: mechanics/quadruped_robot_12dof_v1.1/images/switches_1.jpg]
<br>*Push Button Switches - weight: 3,5g each*<br>  
* E-Stop Switch: red button - normally closed - momentarily open while pushed
* On-Off Switch: green button - normally open - momentarily closed while pushed
* ø13,6mm / weight: 3,5g
* Ordering information [below](#bill-of-materials---upgrade-quadruped-robot-12dof-v11)

### Status Led Ring
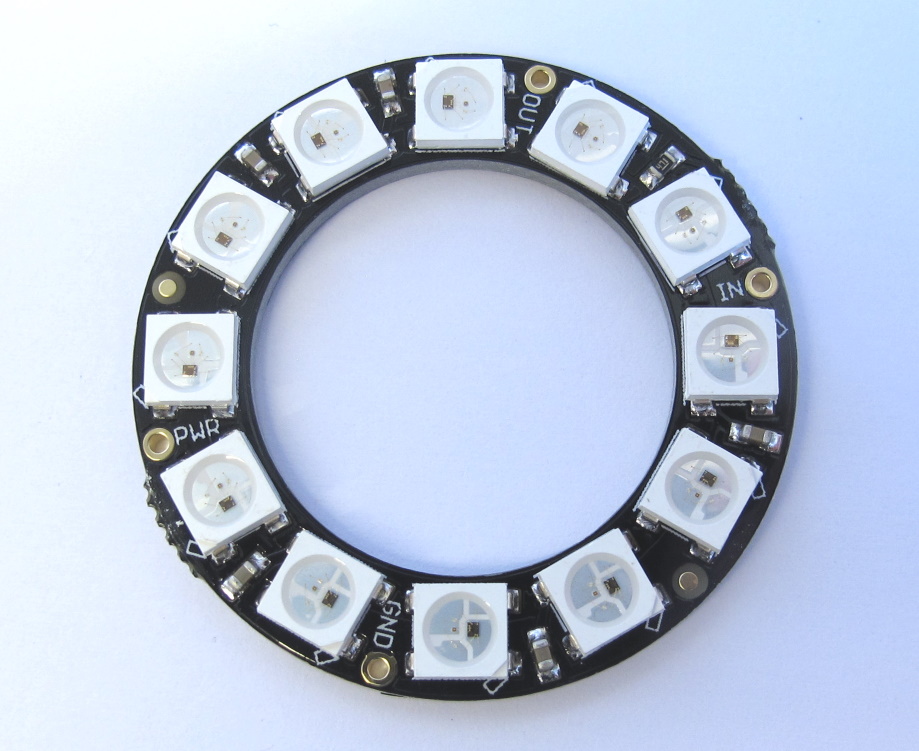
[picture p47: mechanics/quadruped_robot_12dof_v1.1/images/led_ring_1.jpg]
<br>*Status Led Ring - weight: 3,3g*<br>  
* Status Led Ring with 12 Neopixel RGB leds
* dimensions: OD: 36,9mm / ID: 23,3mm
* weight: 3,3g
* Ordering information [below](#bill-of-materials---upgrade-quadruped-robot-12dof-v11)
---
## 3D Printed Parts

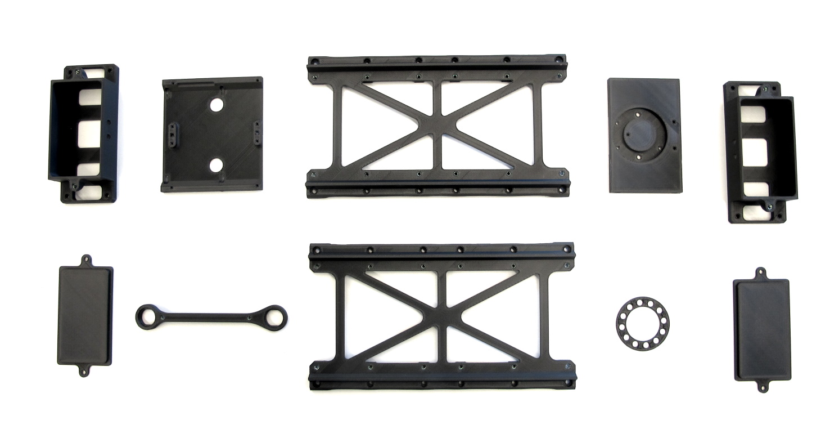
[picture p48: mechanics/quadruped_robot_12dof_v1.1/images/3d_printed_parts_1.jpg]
<br>

* All the STL files for 3d printing the parts below can be found here: [STL Files](stl_files). <br>

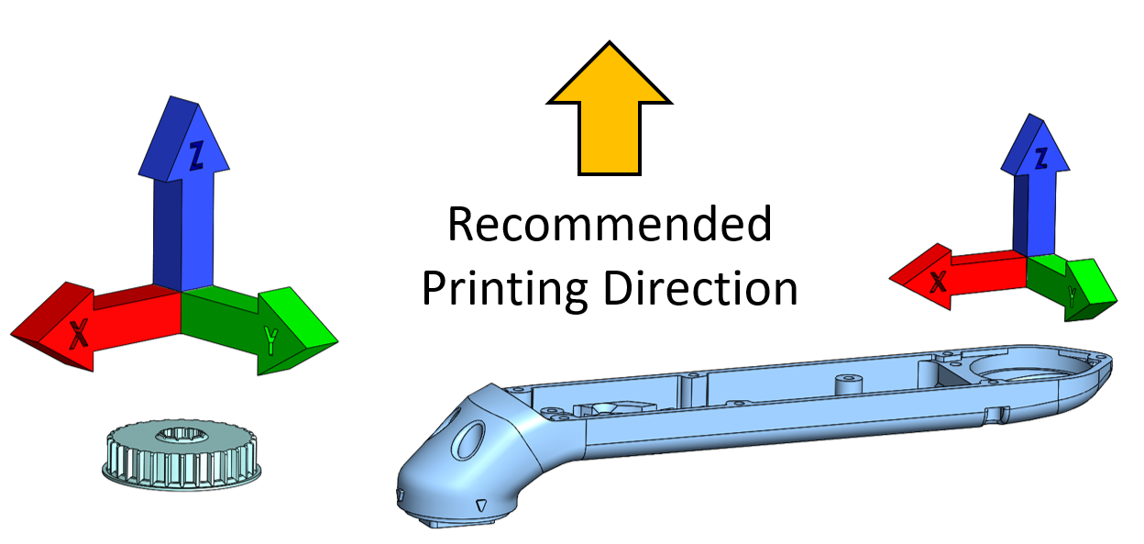
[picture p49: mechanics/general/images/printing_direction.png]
<br>

`The recommended printing direction for all the parts below is the positive z direction of the stl files.`

---
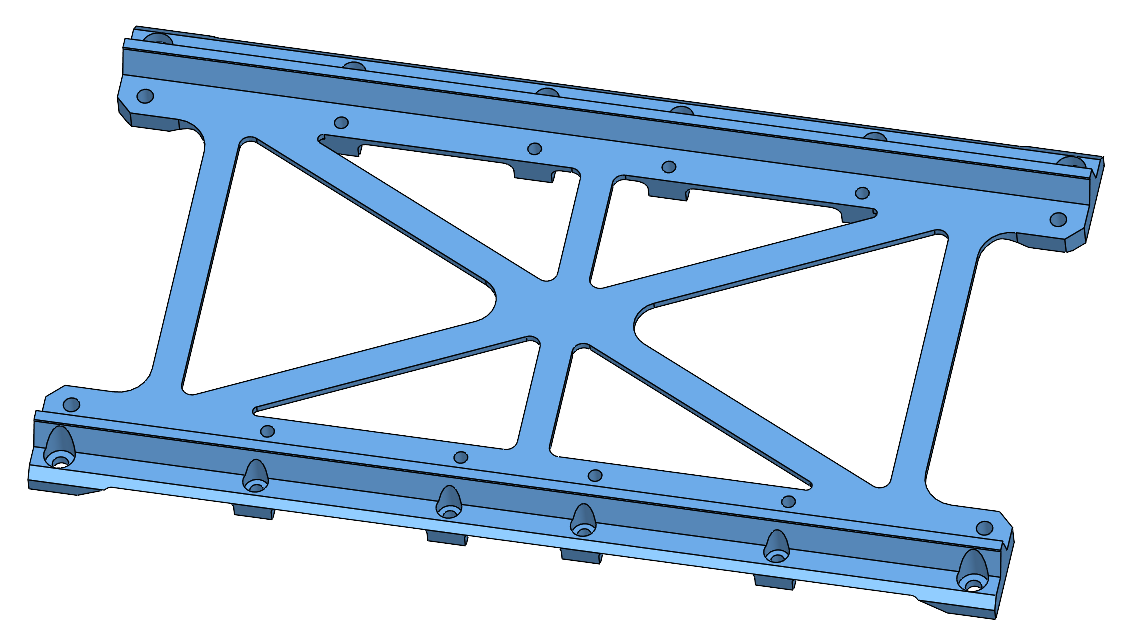
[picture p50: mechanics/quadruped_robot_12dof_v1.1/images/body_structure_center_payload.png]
 <br>
* [Body Structure Center Payload - STL file](stl_files/body_structure_center_payload.STL)<br>
* this part can be used on the top and the bottom side of the robot
* weight: 31g
---
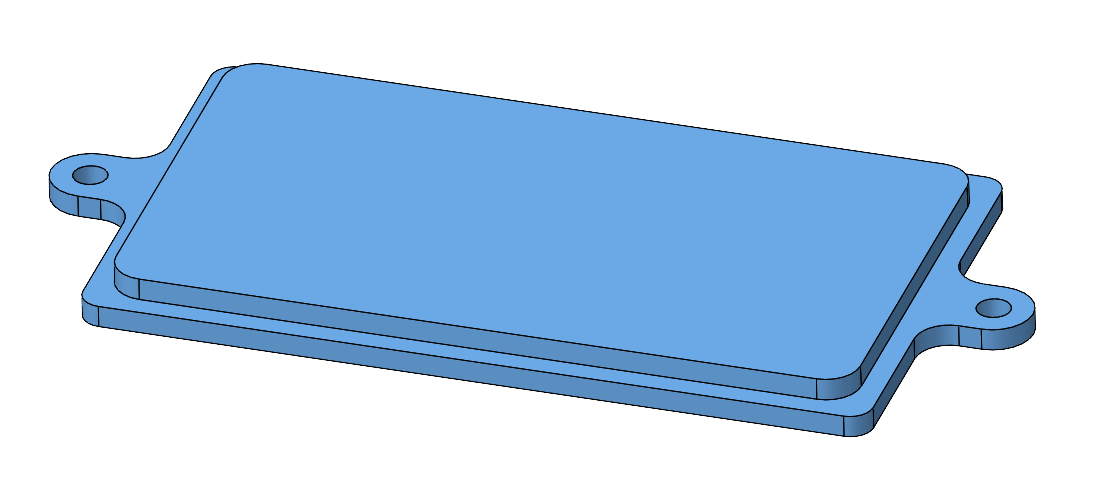
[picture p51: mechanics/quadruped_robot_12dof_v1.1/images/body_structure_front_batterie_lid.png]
 <br>
* [Body Structure Front Batterie Lid - STL file](stl_files/body_structure_front_batterie_lid.STL)<br>
* weight: 11g
---
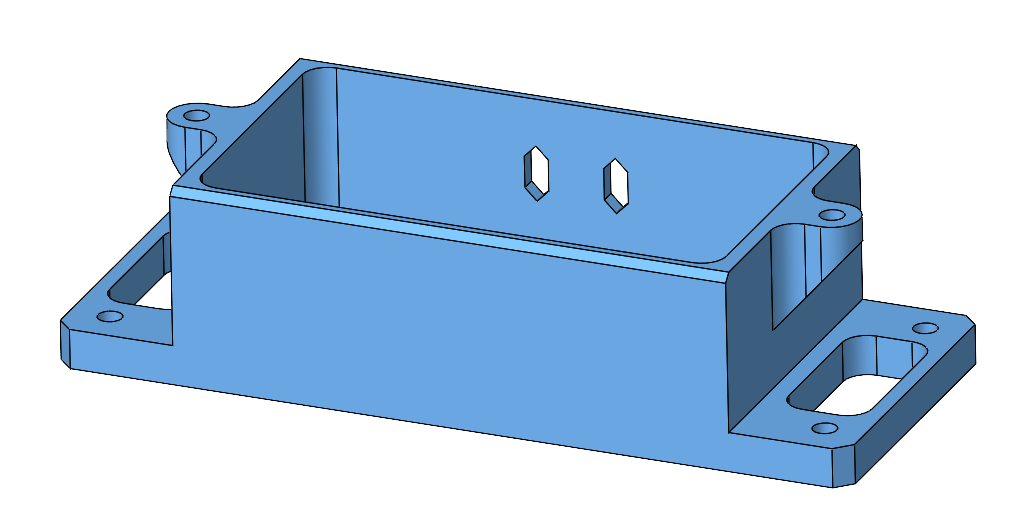
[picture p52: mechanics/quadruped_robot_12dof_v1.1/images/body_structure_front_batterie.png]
 <br>
* [Body Structure Front Batterie - STL file](stl_files/body_structure_front_batterie.STL)<br>
* weight: 18g

---
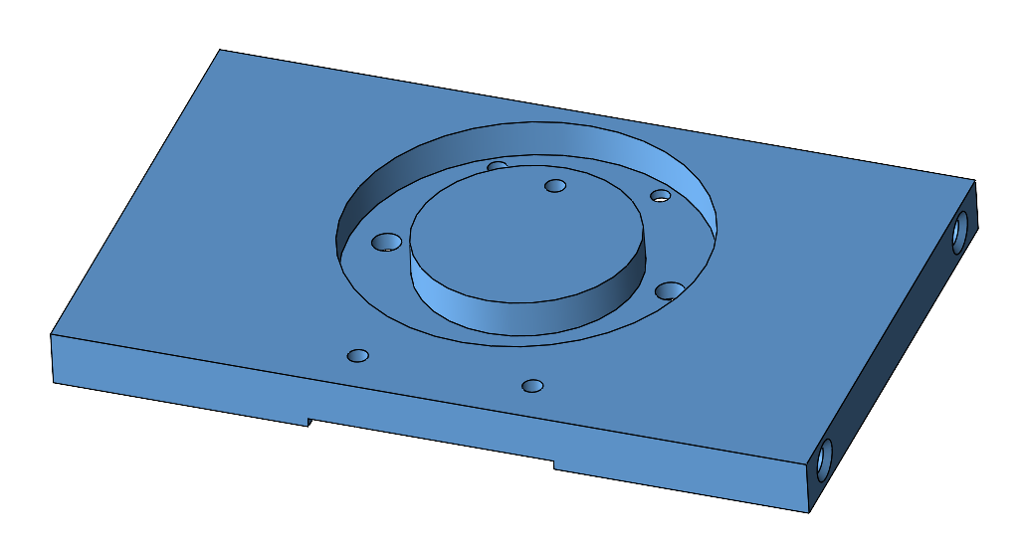
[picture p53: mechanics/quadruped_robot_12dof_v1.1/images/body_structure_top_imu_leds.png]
 <br>
* [Body Structure Top IMU Leds - STL file](stl_files/body_structure_top_imu_leds.STL)<br>
* weight: 15g
---
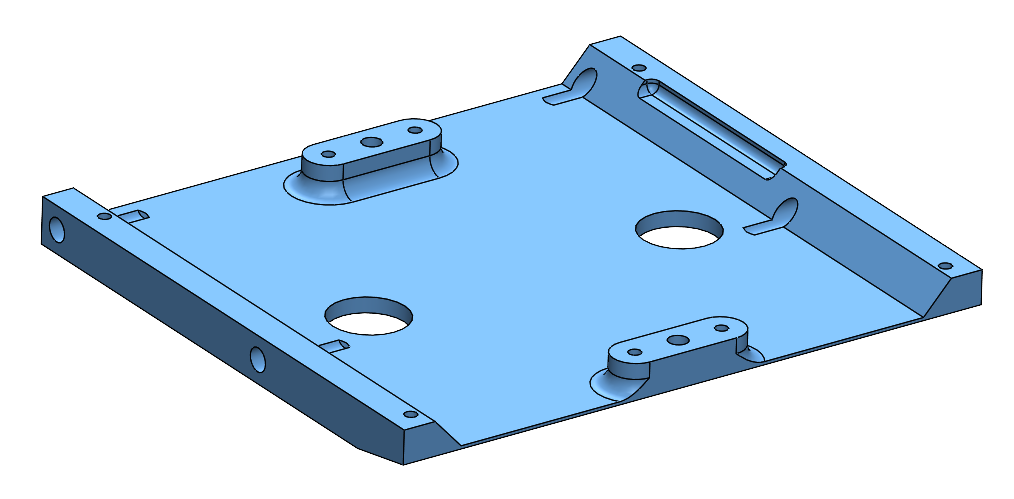
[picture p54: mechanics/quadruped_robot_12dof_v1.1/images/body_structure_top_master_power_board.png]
 <br>
* [Body Structure Top Master Power Board - STL file](stl_files/body_structure_top_master_power_board.STL)<br>
* weight: 15g
---
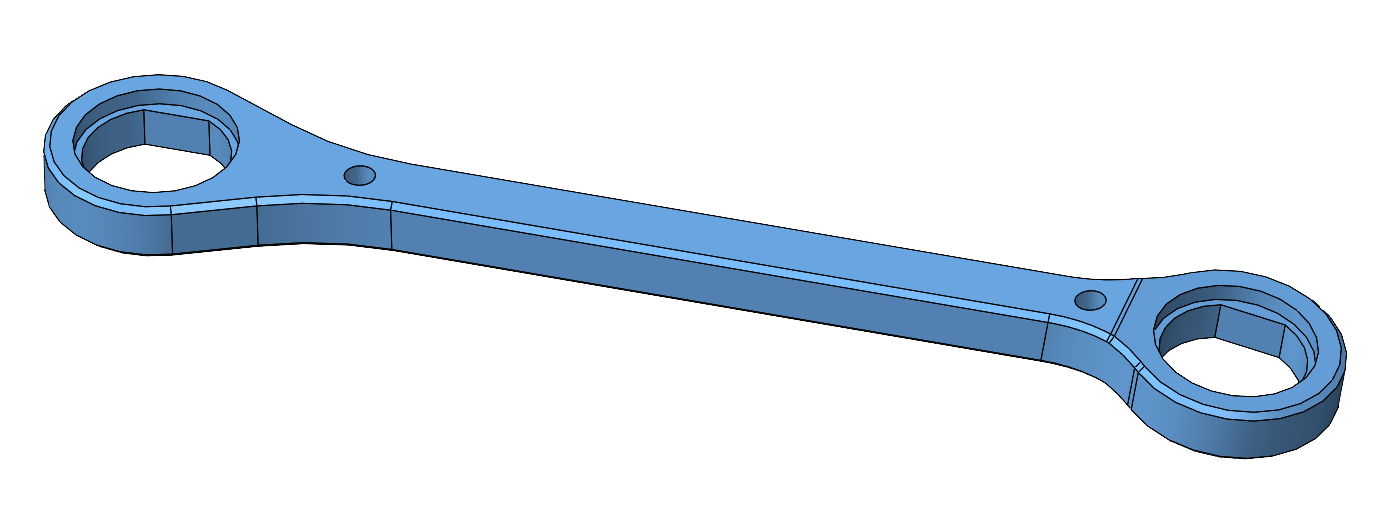
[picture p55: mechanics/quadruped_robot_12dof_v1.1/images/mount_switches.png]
 <br>
* [Mount Switches - STL file](stl_files/mount_switches.STL)<br>
* weight: 4g
---
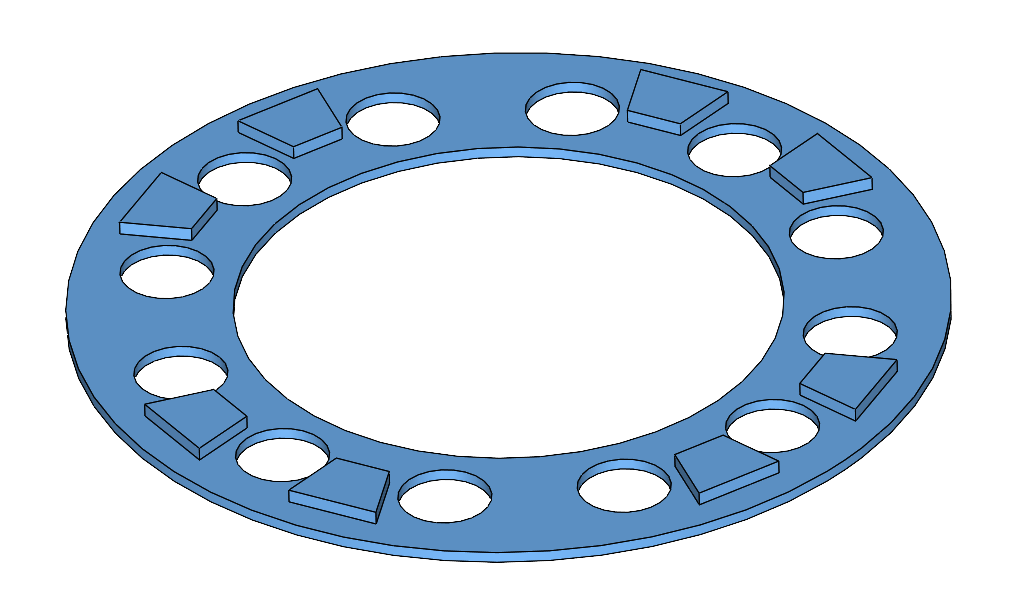
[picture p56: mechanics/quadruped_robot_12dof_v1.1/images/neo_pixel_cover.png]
 <br>
* [Neo Pixel Cover - STL file](stl_files/neo_pixel_cover.STL)<br>
* weight: 0,3g
---

## Bill of Materials - Upgrade Quadruped Robot 12dof v1.1


| Part Name | Quantity | Ordering Information | Comments |  
| --- | --- | --- | --- |
|Power Management Board|1|[Power Board GitHub Page](https://github.com/thomasfla/power-board)|Custom Electronics|
|LiPo Battery SLS X-Cube 850mAh|2|[SLS Product Page](https://www.stefansliposhop.de/en/batteries/sls-x-cube/sls-x-cube-30c/sls-x-cube-850mah-3s1p-11-1v-30c-60c::1534.html)<br>SLSCUX08503130|[Charging and Safey Accessories](../../electronics/details/details_components.md#batteries-and-charging-accessories)|
|E-Stop Switch|1|RS 820-7587|Red Push Button Switch|
|On-Off Switch|1|RS 820-7593|Green Push Button Switch|
|Status Led Ring|1|Adafruit 1643<br>Mouser 485-1643 <br>Conrad 1516560|NeoPixel Ring RGB LED 12 x WS2812|
|Body Structure Center Payload|2|[STL File](stl_files/body_structure_center_payload.STL)|3d printed part|
|Body Structure Front Batterie Lid|2|[STL File](stl_files/body_structure_front_batterie_lid.STL)|3d printed part|
|Body Structure Front Batterie|2|[STL File](stl_files/body_structure_front_batterie.STL)|3d printed part|
|Body Structure Top IMU Leds|1|[STL File](stl_files/body_structure_top_imu_leds.STL)|3d printed part|
|Body Structure Top Master Power Board|1|[STL File](stl_files/body_structure_top_master_power_board.STL)|3d printed part|
|Mount Switches|1|[STL File](stl_files/mount_switches.STL)|3d printed part|
|Neo Pixel Cover|1|[STL File](stl_files/neo_pixel_cover.STL)|3d printed part|
|Fastener M2 x 6 SHCS|8||Power Board and Master Board|
|Fastener M2,5 x 6 SHCS|1||Switch Mount Back|
|Fastener M2,5 x 8 SHCS|1||Switch Mount Front|
|Fastener M3 x 6 SHCS|4||Batterie Lid|
|Helicoil M2,5 x 3,75mm|10|||
|Helicoil M3 x 4,5mm|20|||

---
## Preparing the 3D Printed Parts

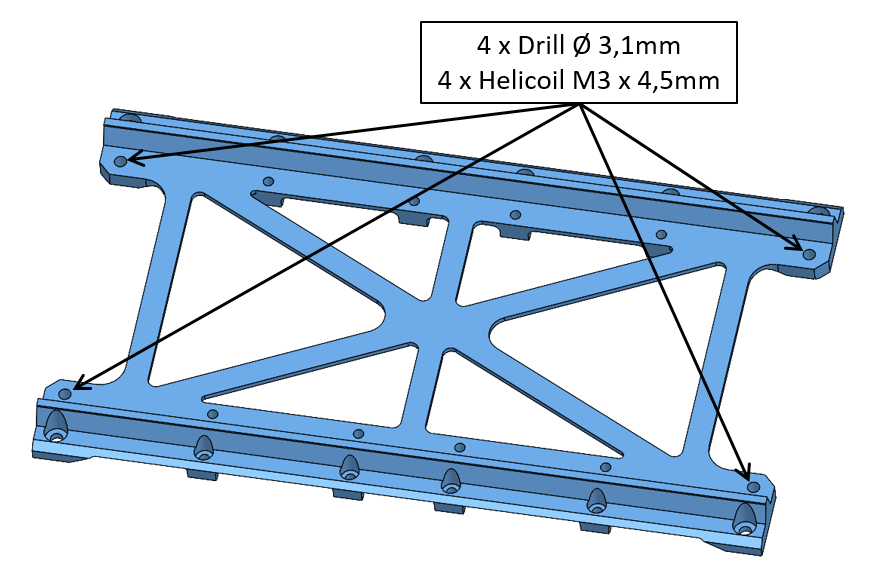
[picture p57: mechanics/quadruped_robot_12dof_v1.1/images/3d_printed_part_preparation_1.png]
<br>

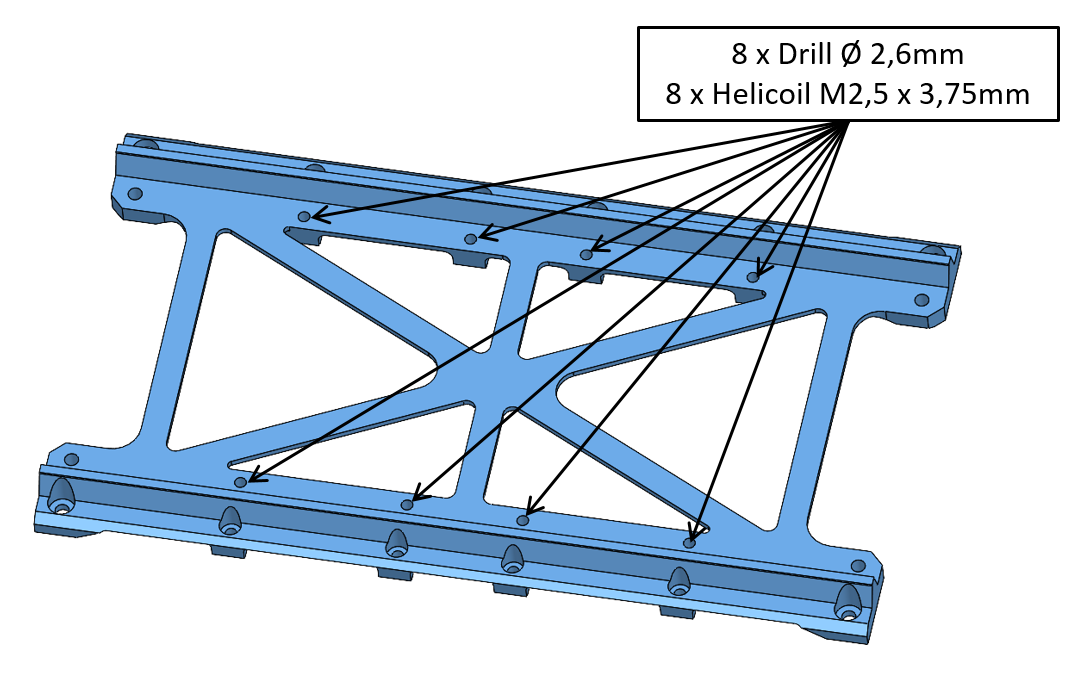
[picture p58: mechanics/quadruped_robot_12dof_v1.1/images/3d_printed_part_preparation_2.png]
<br>

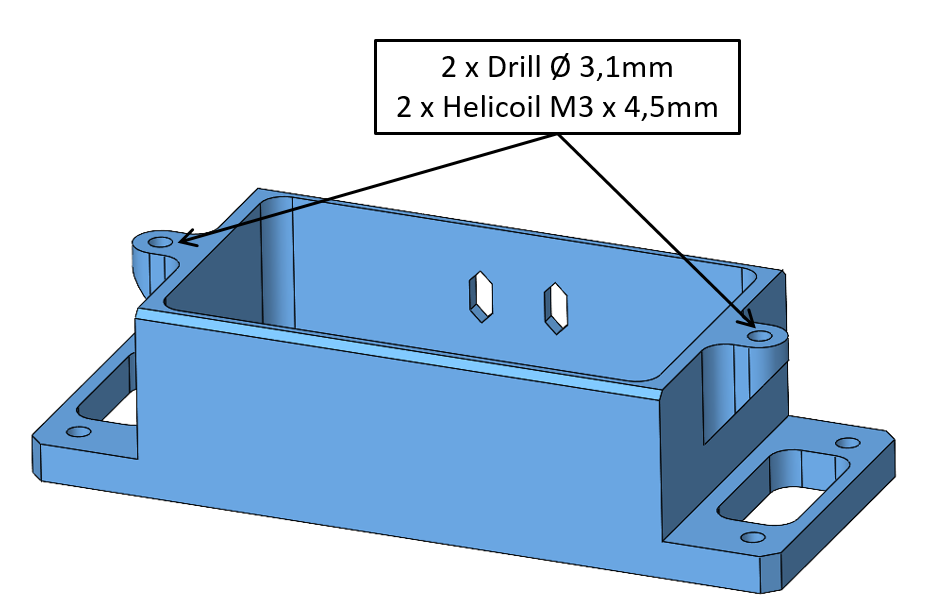
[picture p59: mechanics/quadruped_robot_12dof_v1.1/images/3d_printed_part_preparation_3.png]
<br>

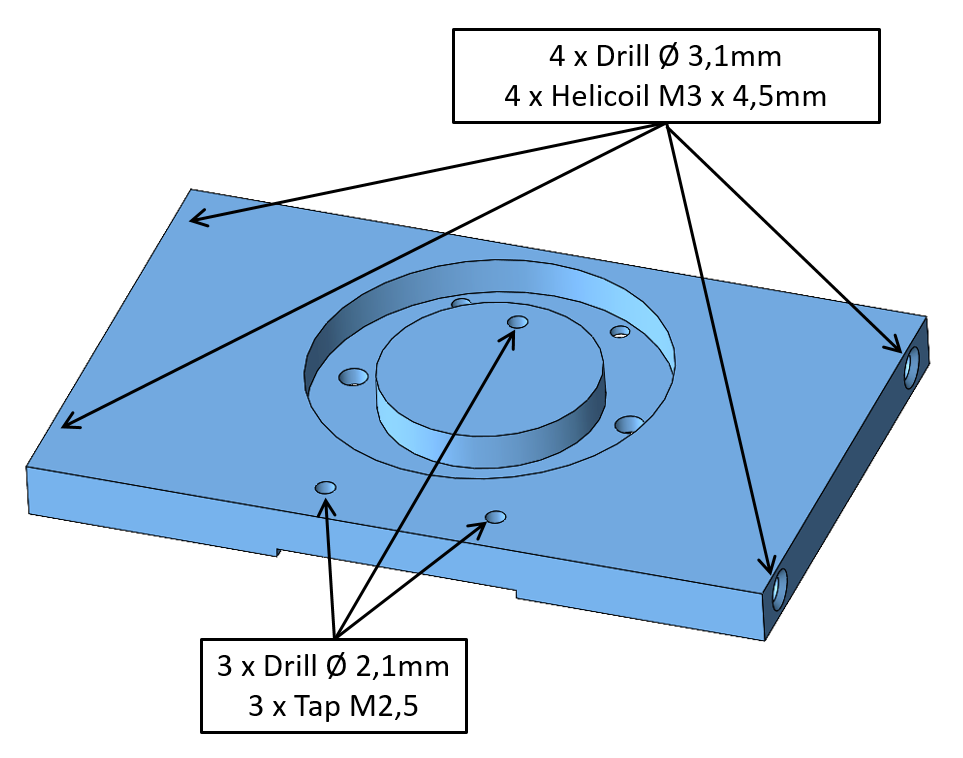
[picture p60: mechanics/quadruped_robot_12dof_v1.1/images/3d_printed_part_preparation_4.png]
<br>

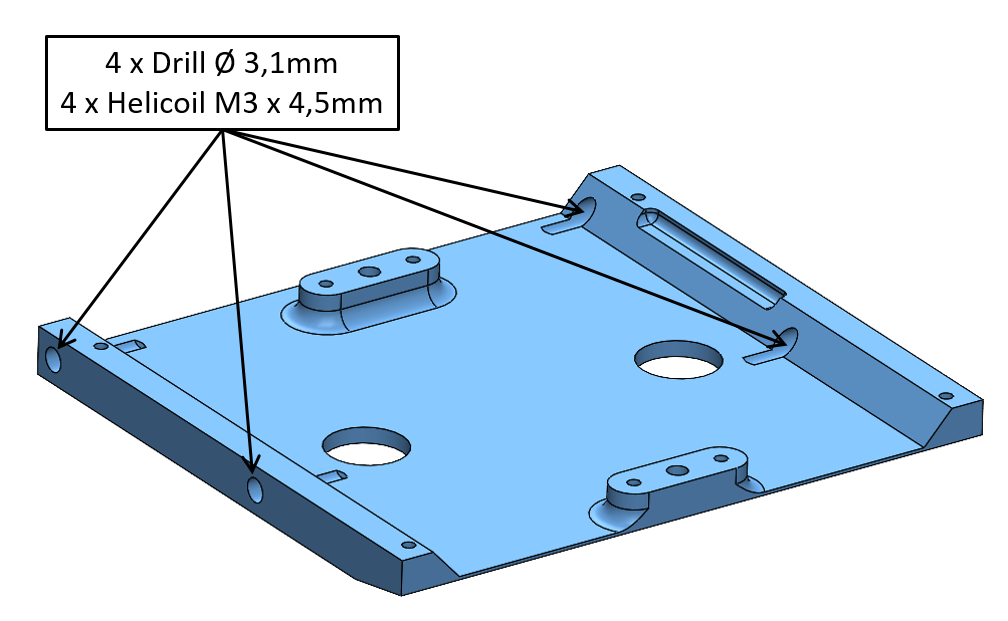
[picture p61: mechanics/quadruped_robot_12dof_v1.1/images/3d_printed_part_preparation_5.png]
<br>

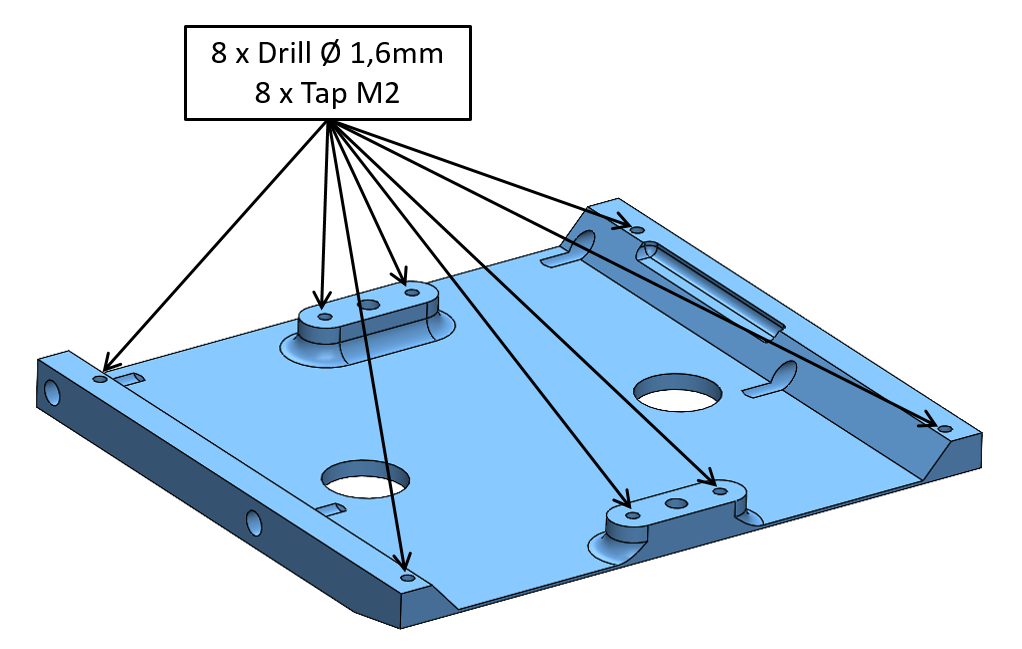
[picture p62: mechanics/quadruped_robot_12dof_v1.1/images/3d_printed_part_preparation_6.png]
<br>

<br>

## Wiring Documentation
### Power Board and Master Board
<br>*Power Board, Master Board and Switches on Mounting plate - weight: 67g*<br>  

| Description | Quantity | Wire Length | Comments |  
| --- | --- | --- | --- |
|Power Wire|1|8cm|[XT30](../../electronics/details/details_components.md#power-connectors) to [2pin Hirose](../../electronics/details/details_components.md#hirose-df13-sockets)| 
|SPI Wire|1|5cm|[SPI Wiring Documentation](../../electronics/details/details_wiring.md#spi-wires)|
|Switch Wire|1||Pin assignment below.|

<br>*Wiring On/Off and E-Stop Switch*<br>

### Front Micro Driver Stack
<br>*Front Micro Driver Stack - fully wired - weight: 112g*<br>  

| Description | Quantity | Wire Length | Comments |  
| --- | --- | --- | --- |
|Motor Phase Wires |18|8cm|[Micro Driver Board Wiring Documentation](../../electronics/details/details_wiring.md#micro-driver-board-wiring)|
|Power Supply Wires|3|30cm|[Micro Driver Board Wiring Documentation](../../electronics/details/details_wiring.md#micro-driver-board-wiring)|
|SPI Wires|3|34cm|[SPI Wiring Documentation](../../electronics/details/details_wiring.md#spi-wires)|

### Hind Motor Driver Stack
<br>*Hind Motor Driver Stack - fully wired - weight: 98g*<br>  

| Description | Quantity | Wire Length | Comments |  
| --- | --- | --- | --- |
|Motor Phase Wires |18|8cm|[Micro Driver Board Wiring Documentation](../../electronics/details/details_wiring.md#micro-driver-board-wiring)|
|Power Supply Wires|3|16cm|[Micro Driver Board Wiring Documentation](../../electronics/details/details_wiring.md#micro-driver-board-wiring)|
|SPI Wires|3|18cm|[SPI Wiring Documentation](../../electronics/details/details_wiring.md#spi-wires)|

### Inertia Measurement Unit
<br>*Inertia Measurement Unit - weight: 18g*<br>  

| Description | Quantity | Wire Length | Comments |  
| --- | --- | --- | --- |
|Interface Wire |1|40cm|[IMU Wiring Documentation](../../electronics/details/details_wiring.md#imu-wire)|

### Neo Pixel Led Ring
<br>*Neo Pixel Led Ring with Mounting Plate - weight: 22g*<br>  

| Description | Quantity | Wire Length | Comments |  
| --- | --- | --- | --- |
|Interface Wire |1|34cm|Pin assignment below.|

<br>*Neo Pixel Interface Wire*<br>  

### Battery Wire

<br>*Battery Wire - weight: 12g*<br>  

<br>*Battery wire - the batteries are connected in series.*<br>

## More Information
[Open Dynamic Robot Initiative - Webpage](https://open-dynamic-robot-initiative.github.io)  
[Open Dynamic Robot Initiative - YouTube Channel](https://www.youtube.com/channel/UCx32JW2oIrax47Gjq8zNI-w)   
[Open Dynamic Robot Initiative - Forum](https://odri.discourse.group/categories)  
[Open Dynamic Robot Initiative - Paper](https://arxiv.org/pdf/1910.00093.pdf)  
[Hardware Overview](../../README.md#open-robot-actuator-hardware)  
[Software Overview](https://github.com/open-dynamic-robot-initiative/open-dynamic-robot-initiative.github.io/wiki)  

## Authors
Felix Grimminger

## License
BSD 3-Clause License

## Copyright
Copyright (c) 2019-2021, Max Planck Gesellschaft and New York University

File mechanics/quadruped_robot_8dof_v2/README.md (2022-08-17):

# Quadruped Robot 8dof v2

<br>*Quadruped Robot 8dof v2 - weight 1,9kg*  

## Description
* weight reduced body frame structure and new electronics
* 8dof - 8 degree of freedom robot
* Power and communication over wire (24V / Ethernet)
* Master board, micro drivers and inertia measurement unit
* Robot weight 1,7kg
* We are adding 200g weights as placeholder for batteries
* Weight 1,9kg with 200g battery placeholders

<br>*Quadruped robot without top structure*  

<br>*Quadruped robot standing*

---
## Electronics
### Master Board
 <br> *Master board v2 - weight: 19g*
* Custom electronics board -> [Master Board Documentation](https://github.com/open-dynamic-robot-initiative/master-board#master-board)
---
### Micro Driver Electronics
 <br> *Micro Driver v2 - Stack with 2 cards - weight: 32g*

* each micro driver board controls 2 brushless motors
* there is a stack with 2 cards in the front and in the back of the robot
* Custom electronics board -> [Micro Driver Board Documentation](../../electronics/micro_driver_electronics/README.md)
---
### Inertia Measurement Unit
 <br>
* Lord Microstrain 3DM-CX5-25
* Weight: 13g
* [Lord Microstrain webpage](https://www.microstrain.com/inertial/3dm-cx5-25)
* We use the imu with an extended measurement range
  * Gyro Rate: +/- 900 deg/sec.
  * Accelerometer range: +/- 20G
---
## 3D Printed Parts
<br>*Body structure part overview - the weight of the parts in the picture is 226g.* <br>

<br>*Body structure assembled - weight: 247g* <br>

 <br>

`The recommended printing direction for all the parts below is the positive z direction of the stl files.`

* All the STL files for 3d printing the body structure can be found here: [STL Files Body Structure](stl_files). <br>

---
 <br>
* [Body Structure Bottom - STL file](stl_files/body_structure_bottom.STL)<br>
* weight: 38g
---
 <br>
* [Body Structure Front - STL file](stl_files/body_structure_front.STL)<br>
* weight: 24g
* the front and back plates of the body are identical
---
 <br>
* [Body Structure Side - STL file](stl_files/body_structure_side.STL)<br>
* weight: 52g
* the left and right side body structures are identical
---
 <br>
* [Body Structure Top - STL file](stl_files/body_structure_top.STL)<br>
* weight: 35g
---
 <br>
* [Body Structure Top Vicon- STL file](stl_files/body_structure_top_vicon.STL)<br>
* weight: 37g
* attachment points for Vicon markers
---
 <br>
* [Body Structure Top Roll Bar- STL file](stl_files/body_structure_top_roll_bar.STL)<br>
* weight: 55g
* attachment points for Vicon markers
* roll bars for protecting the Vicon markers
---
 <br>
* [Spacer Micro Driver Stack 12mm- STL file](stl_files/spacer_micro_driver_stack_12mm.STL)<br>
---

 <br>
* [Stand Adapter - STL file](stl_files/stand_adapter.STL)<br>
---

## Bill of Materials - Quadruped Robot 8dof v2


| Part Name | Quantity | Ordering Information | Comments |  
| --- | --- | --- | --- |
|2DOF Leg |4|Custom assembly|[2DOF Leg Documentation](../leg_2dof_v2/README.md)|
|Body Structure Bottom |1|[STL file](stl_files/body_structure_bottom.STL)|3d printed part|
|Body Structure Front |2|[STL file](stl_files/body_structure_front.STL)|3d printed part<br>The front and back plates are identical.|
|Body Structure Side |2|[STL file](stl_files/body_structure_side.STL)|3d printed part<br>The left and right side plates are identical.|
|Body Structure Top |1|[STL file](stl_files/body_structure_top.STL)|3d printed part|
|Spacer Micro Driver Stack 12mm |8|[STL file](stl_files/spacer_micro_driver_stack_12mm.STL)|3d printed part|
|Stand Adapter |1|[STL file](stl_files/stand_adapter.STL)|3d printed part<br>(optional)|
| Inertia Measurement Unit | 1 | Lord Microstrain<br> 3DM-CX5-25| Extended measurement range<br> Gyro Rate: +/- 900 deg/sec. Accelerometer range: +/- 20G|
| Master Board v2 | 1 | [Master Board Documentation](https://github.com/open-dynamic-robot-initiative/master-board#master-board) | Custom Electronics |
| Micro Driver Board v2 | 4 | [Micro Driver Documentation](../../electronics/micro_driver_electronics/README.md)  | Custom electronics |
|Fasteners Body Structure |25|M3x8 Socket Head Cap Screw|Stainless steel|
|Fasteners Legs to Front Plate|8|M3x12 Socket Head Cap Screw|Stainless steel|
|Fasteners Micro Driver Electronics|8|M2,5x20 Socket Head Cap Screw|Stainless steel|
|Fasteners Master Board|3|M2x6 Socket Head Cap Screw|Stainless steel|
|Fasteners IMU|3|M2,5x16 Slotted Screw<br>Conrad 839940-62|Polyamide Plastic|
|Helicoil Threaded Inserts|25|M3x4,5 Helicoil<br>||
Helicoil Threaded Inserts|8|M3x6 Helicoil<br>||

## Robot Coordinate System Origin
 <br>

## Inertial Sensor Origin Position
 <br>

* the inertial sensor origin is not in the geometrical center of the IMU
* [IMU Technical Drawing - see Page 2](https://s3.amazonaws.com/download.microstrain.com/Drawings/3065-0291-ICD.pdf)

|IMU Origin Position in the<br>Robot Coordinate System| X | Y | Z |  
| --- | --- | --- | --- |
||-10,18mm|-38,35mm|-7,85mm|

## Simplified 3D Model

The simplified STL files for visualization and simulation can be found here: [STL Files Visualization](stl_files_for_visualization)



<br>*Click on picture above to view the PDF drawing*

## Quadruped Inertia Parameters for Simulation
<br>*Quadruped Inertia Parameters - Click on picture to view PDF document.*<br>

## Quadruped 8dof Wiring
More wiring information: [Details Wiring](../../electronics/details/details_wiring.md#details-wiring)

### Actuator Module Wires
| Description | Quantity | Wire Length | Comments |  
| --- | --- | --- | --- |
|Hip FE Motor Phases |3|6cm|FRHFE, FLHFE, HRHFE and HLHFE |
|Hip FE Encoder Wire |1|10cm|FRHFE, FLHFE, HRHFE and HLHFE|
|Knee Motor Phases |3|12cm|FRK, FLK, HRK and HLK |
|Knee Encoder Wire |1|19cm|FRK, FLK, HRK and HLK|

### SPI Wires
| Description | Quantity | Wire Length | Comments |  
| --- | --- | --- | --- |
|SPI Wire |1|16cm| #0 - FLHFE and FLK|
|SPI Wire |1|16cm| #1 - FRHFE and FRK|
|SPI Wire |1|20cm| #2 - HLHFE and HLK |
|SPI Wire |1|14cm| #3 - HRHFE and HRK|

### Micro Driver Wires
| Description | Quantity | Wire Length | Comments |  
| --- | --- | --- | --- |
|Motor Phase Wires |24|7cm||

## Robot Stand
 <br><br>

| Part Name | Quantity | Ordering Information | Comments |  
| --- | --- | --- | --- |
|Stand Adapter |1|[STL file](stl_files/stand_adapter.STL)|3d printed part|
|Pin 3mm x 36mm |1|||
|Slotted Aluminum Profile<br>Length 40cm |2|Item part number: 0.0.026.33|  Item Size 8 - 40mm x 40mm|
|Slotted Aluminum Profile<br>Length 20cm |2|Item part number: 0.0.026.33|  Item Size 8 - 40mm x 40mm|
|90 Degree  Angle Brackets|4|Item part number: 0.0.411.15|Item Size 8 |
|End Caps |4|Item part number: 0.0.026.01|Item Size 8 - 40mm x 40mm |

## Vicon Object

 <br>*Vicon Object - weight 48g* <br>

| Part Name | Quantity | Ordering Information | Comments |  
| --- | --- | --- | --- |
|Body Structure Top Vicon |1|[STL file](stl_files/body_structure_top_vicon.STL)|3d printed part|
|Helicoil Threaded Inserts|8|M3x4,5 Helicoil<br>||
|Vicon Markers |9|9,5mm diameter||
|Fasteners Vicon Markers |9|M4x10 Set Screw|Stainless Steel|

 <br>*Vicon Marker Posititions*

* You can download the Vicon object here: [Quadruped 8dof v2 Vicon Object](details/quadruped_8dof_v2_vicon_object.zip)

---
## Preparing the 3d printed parts

<br>*Body Structure Side*

---
<br>*Body Structure Top*

---
<br>*Body Structure Top with Vicon marker attachments*

---
<br>*Body Structure Bottom - Helicoils*

---
<br>*Body Structure Bottom - tapped holes for electronics*

---
## Fasteners Quadruped Body Structure
<br>*Fasteners Body Structure - use the same fasteners on the opposite side.*

---
<br>*Fasteners Body Structure - use the same fasteners on the opposite side.*

---
<br>*Fasteners electronic components.*

---
## View the quadruped cad model in your web browser <br>

<br> *Quadruped Robot 8dof v2 <br> Click on the picture to view the cad model in your browser*

<br> *Quadruped Robot 8dof v2 folded <br> Click on the picture to view the cad model in your browser*

---
## More Information
[Open Dynamic Robot Initiative - Webpage](https://open-dynamic-robot-initiative.github.io)  
[Open Dynamic Robot Initiative - YouTube Channel](https://www.youtube.com/channel/UCx32JW2oIrax47Gjq8zNI-w)   
[Open Dynamic Robot Initiative - Forum](https://odri.discourse.group/categories)  
[Open Dynamic Robot Initiative - Paper](https://arxiv.org/pdf/1910.00093.pdf)  
[Hardware Overview](../../README.md#open-robot-actuator-hardware)  
[Software Overview](https://github.com/open-dynamic-robot-initiative/open-dynamic-robot-initiative.github.io/wiki)  

---
## Authors
Felix Grimminger

## License
BSD 3-Clause License

## Copyright
Copyright (c) 2019-2022, Max Planck Gesellschaft and New York University

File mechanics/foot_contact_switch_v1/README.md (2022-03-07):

# Foot Contact Switch v1
 <br>*Working principle of the optical foot contact switch*

## Description
We designed simple, low cost, lightweight and robust optical foot contact switch for our [quadruped robot.](../quadruped_robot_8dof_v1#quadruped-robot-8dof-v1)  
The contact switch consists of a spring loaded aperture that is located between a led light source and a light sensor.  
External loads displace the aperture and change the light intensity measured by the sensor.  
For centering the foot we use 12 elastic silicone elements (6 on each side).



The foot contact switch is symmetric and can detect forces from a wide range of different angles (270 degrees).  
For visual feedback and monitoring there are bi-color leds mounted on each side of the foot.

<br>*Left side: Foot Contact Switch loaded / Right side: Foot Contact Switch unloaded*

## Lower Leg and Foot Contact Switch
 <br>*Lower Leg and Foot Contact Switch Component Overview*

 <br>*Lower Leg and Foot Contact Switch assembled - weight: 35g*

The weight of the foot, the contact switch electronics and the silicone elements is about 10g.  
To prevent the foot from rotating we use a steel pin that is guided by the lower leg structure.   
Under load the foot deflects up to 2mm from its neutral position.  
The electronics are supplied with 3.3V and generate an analog output signal between 3V and 0V.  
The signal is converted by the microcontroller ADC and transmitted over CAN at 1kHz.  
We measured the delay of the foot contact switch with respect to a ATI Mini40 force sensor for a drop of the 2dof leg from a height of 8cm.   
The measured delay between the ATI force sensor signal and the foot contact signal was 2ms.  
The data was logged at 1kHz using a Realtime Linux PC.

<br>*Foot Contact Switch Electronics*

## Video
Foot Sensor Video (https://www.youtube.com/watch?v=1TluBZRFed8)

## Sensor Characteristics
 <br>
* x-axis -> vertical force [N] measured with ATI Mini40 Sensor  
* y-axis -> foot contact sensor ouput signal inverted and normalized
* 0-1 on the y-axis corresponds to 3V - 0V range

## Off-the-shelf Components
### Silicone Tube
<br>

* Silicone tube - outer diameter: 6mm / inner diameter: 4mm / length: 3mm  
* 12 elements / 6 on each side
* a [tube cutter](../actuator_module_v1/details/details_tools.md#tube-cutter) can be used to prepare the segments

### Bicycle Tire
<br>

* a bicycle tire segment is bonded to the surface of the foot
* we use Schwalbe Lugano 28" 23-622 tire
* cut to 65mm x 10mm pieces
* bond to the foot with [Loctite 406](../actuator_module_v1/details/details_tools.md#loctite)
* [Instructions Foot Preparation](../general/lower_legs.md#preparing-the-lower-legs)

### Fasteners
<br>

* Steel Pin 1,5mm x 12mm  
* Socket Head Cap Screws M2,5x6
* Helicoil Thread Inserts M2,5 x 3.75mm

## 3D Printed Parts
 <br>

`The recommended printing direction for all the parts below is the positive z direction of the stl files.`

The STL files for 3d printing the parts are available in the [STL folder](stl_files).

 <br>
* [Lower Leg Structure Base - 18g](stl_files/lower_leg_structure_base.STL)
* FDM or SLS printer

 <br>
* [Lower Leg Structure Fork - 5g](stl_files/lower_leg_structure_fork.STL)
* FDM or SLS printer

 <br>
* [Foot Structure - 3.4g](stl_files/foot_structure.STL)
* SLA printer - Accura Extreme Gray

## Custom Electronic Boards
The foot contact switch consists of two boards with traces and components on all four sides.  
The diameter of the electronics boards is 10mm.  

 <br>*Foot Contact Switch Main Board  - Left: Outer side / Right: Inner Side*

 <br>*Foot Contact Switch Satellite Board  - Left: Outer side / Right: Inner Side*

## Light Sensor Offset
 <br>*Picture Light Sensor - the sensitive area is not in the center of the component*
* note that the sensing area of the light sensor is not in the geometrical center of the component
* when we solder the light sensor we use a microscope to align the sensing area of the sensor with the center of the board

## Switching Voltage for the Indicator Leds
 <br>*Schematic - voltage divider for switching the indicator leds*

* the switching voltage for the indicator leds on the foot is set by the voltage divider R4 and R5
* we use 10kΩ for R4 and 20kΩ for R5 resulting in a switching voltage of 2.2V
* you can adjust the switching voltage by changing the ratio of the voltage divider
* the switching voltage threshold is only used for the indicator leds
* the microcontroller receives the full range analog signal
* that means that you can set the threshold on the software side independently

## Details Foot Contact Switch
Special thanks to Joshi Walzog for designing and manufacturing the electronics boards!

* [Bill Of Materials Foot Contact Switch - PDF Document](documentation/bom_foot_contact_switch_v1.pdf)
* [Bill Of Materials - Excel Document](documentation/bom_foot_contact_switch_v1.xlsx)  
* [Eagle Files - Zipped Folder](documentation/eagle_files.zip)
* [Gerber Files - Zipped Folder](documentation/gerber_files.zip)

To view the Eagle files you need to download the free [Eagle PCB Design Software](https://www.autodesk.com/products/eagle/free-download#) for Windows, Mac and Linux.

## Foot Contact Switch Wiring
 <br>*Foot Contact Switch Connectors and Wiring*

## Alternative Lower Leg Versions

 <br>  

* alternative lower leg versions without contact sensor are documented here: [Lower Leg Documentation](../general/lower_legs.md#lower-legs)

## PDF Drawing
<br> *Foot Contact Switch Overview - Click on the picture to view the PDF drawing*

## View the foot contact switch cad model in your web browser
<br> *Foot Contact Switch - Click on the picture to view the cad model in your browser*

## More Information
[Open Dynamic Robot Initiative - Webpage](https://open-dynamic-robot-initiative.github.io)  
[Open Dynamic Robot Initiative - YouTube Channel](https://www.youtube.com/channel/UCx32JW2oIrax47Gjq8zNI-w)   
[Open Dynamic Robot Initiative - Forum](https://odri.discourse.group/categories)  
[Open Dynamic Robot Initiative - Paper](https://arxiv.org/pdf/1910.00093.pdf)  
[Hardware Overview](../../README.md#open-robot-actuator-hardware)  
[Software Overview](https://github.com/open-dynamic-robot-initiative/open-dynamic-robot-initiative.github.io/wiki)  

## Authors
Felix Grimminger

## License
BSD 3-Clause License

## Copyright
Copyright (c) 2019-2022, Max Planck Gesellschaft and New York University

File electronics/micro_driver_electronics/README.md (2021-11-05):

# Micro Driver Electronics

<br> <br>

* dual brushless motor driver electronics
* performs torque control at 10kHz for each motor
* miniaturized version of the [Texas Instruments Evaluation Boards](../ti_electronics/README.md#texas-instruments-evaluation-board-electronics)
* SPI communication with [Master Board](https://github.com/open-dynamic-robot-initiative/master-board#master-board) at 1kHz
* 6 layer board / FR4 / copper thickness 35μm
* Dimensions: 51mm x 50mm
* Weight: 13g
* input voltage: 5V - 32V (we operate our robots at 24V)

## LED status
GREEN/BLUE LED (shows system and motor status):<br>
Off = system disabled<br>
On =system enabled<br>
Slow Blinking = motor enabled<br>
Fast Blinking = aligning motor<br>

RED LED: Turn on if there is an error

## Motor Driver Electronics Comparison
<br> <br>

## Eagle Design Files
<br>

* [MicroDriver v2 Eagle Design Files - microDriver_v2.zip](eagle_design_files/microDriver_v2.zip)

<br><br> <br>

---
## Production Gerber Set and Assembly Packet
* [MicroDriver v2 Gerber Set - microDriver_v2_gerber.zip](production_files/microDriver_v2_gerber.zip)

* [MicroDriver v2 Assembly Packet - microDriver_v2_assembly.zip](production_files/microDriver_v2_assembly.zip)

<br><br> <br>

## Ordering Instructions
### Beta Layout
We have mostly been ordering the Micro Driver boards from [BetaLayout](https://us.beta-layout.com/pcb/).
Beta Layout has the permission to replicate our MicroDriver v2 board order for anybody who is interested - they ship worldwide.

Send an email to info.de@beta-layout.com and ask for a quote for replicating the MicroDriver v2 boards according to the order number **AU-201909/38760**.

They will send you a quote for producing the boards and for the placing and soldering service *- NOT including the cost of the electronic components.*

After you have placed the order for the boards Beta Layout will search for the components and will send you the component list with the actual component prices for your approval. For our last orders the component price was around 50€ per board.

We order the boards with all the components placed and soldered - except for the precision resistors and the Hirose connectors. The soldering of those components is described [below](#soldering-work).

### MacroFab

In the US we have also successfully ordered the Micro Driver Boards from [MacroFab](https://macrofab.com/).

---
## Bill of Materials
### Micro Driver Boards
<br> <br>

|Description|Details|Ordering Information|Comments|
|---|---|---|---|
|MicroDriver v2||[BetaLayout](https://us.beta-layout.com/pcb/)<br> USA: [MacroFab](https://macrofab.com/)|[Ordering Instructions](#ordering-instructions)|
|Precision Resistors 7mΩ ±1%|CRE2512-FZ-R007E-3|RS 824-0348<br>Mouser 652-CRE2512FZR007E-3 |Phase Current Measurement Micro Driver Board|
|Right Angle Pin Header|Pitch 2.54mm|RS 360-6364 |Motor Phase and Power Connection Micro Driver Board|
|Hirose DF13 Right Angle Header 5 Pin|DF13-5P-1.25DS(20)|Digi-Key H2202-ND|Encoder and SPI connector Micro Driver Board. We use the [right angle connectors](../details/details_components.md#hirose-df13-right-angle-pin-headers). Alternatively you can use the [straight connectors](../details/details_components.md#hirose-df13-straight-pin-headers).|

### Flash Adapter and Flash Wire
<br> <br>

|Description|Details|Ordering Information|Comments|
|---|---|---|---|
|JTAG EMULATOR XDS100V2 USB|Spectrum Digital XDS100V2 JTAG|Digi Key 702302-ND<br> Farnell 1831927||
|Pin Header 8 Position 1.27mm pitch|Amphenol ICC 20021111-00008T4LF|Digi-Key 609-3711-ND|Flash Cable Connector Micro Driver Side|
|Pin Header 2,54 mm pitch|Assmann AWL254-DG-G72A|RS 674-2347|Flash Cable Connector Emulator Side|
|Ribbon Cable|HARTING 09180107001|DigiKey 1195-4452-ND|Pitch 1,27mm / 0,050" |

---
# Soldering Work

The MicroDrivers come without any connectors (for power wires, encoders, spi and motor wires). These have to been added. In addition, six resistors have to been soldered on the back of the MicroDriver.

For the encoder connectors, it's possible to use either [Hirose DF13 Straight Pin Headers](../details/details_components.md#hirose-df13-straight-pin-headers) or the [Hirose DF13 Right Angle Pin Headers](../details/details_components.md#hirose-df13-right-angle-pin-headers)

## Resistor Soldering
The six [precision resistors](../details/details_components.md#precision-resistors) needs to be soldered on the back of the MicroDriver.<br>
**Trick:** Use some solder at the tip to initially fix the resistor a bit. Then solder the other side and fix the initial side in the end properly.

<br>

<br>

<br>

## Hirose Connector Soldering

<br>*Micro Driver Stack with right angle Hirose connectors.*<br>

We recommend to use the right angle Hirose connectors for the encoders and the SPI communication if the cards are mounted in a stack. This allows for connecting and disconnecting the encoder and SPI wires without disassembling the stack.

The **right angle Hirose connectors** are mounted to the **bottom side** of the micro driver boards as shown in the picture below.
The **straight Hirose connectors** are mounted on the **top side** of the micro driver boards. That way the pin assignment is identical and both connector options are compatible with the [Actuator Module Wiring Interface](../details/details_wiring.md#actuator-module-wiring).

<br>*Micro Driver Boards with Hirose encoder connectors.<br>Left side: right angle connectors / Right side: straight connectors*<br>

<br>*Micro Driver Boards with Hirose connector for SPI communication.<br>Left side: right angle connectors / Right side: straight connectors*<br>

<br>*Use a vise to clamp the board and locate the Hirose connector.*<br>

<br>*Solder the two encoder connectors and the spi connector onto the board.*<br>

## Motor / Power Wire Soldering

<br>*Solder a two pin right angle connector to the power terminals.*<br>

<br>*Shorten the pins, solder the extension wires and apply heat shrink.*<br>

<br>*Right angle pin and mating connector.*<br>

<br>*Use a mating connector to hold the pin during soldering.*<br>

<br>*Orient the pin as desired, apply solder and shorten the pins.*<br>

<br>*Repeat for all six motor phase connections.*<br>

<br>*Apply the extension wires and heat shrink.*<br>

<br>*Attach the [2mm motor phase connectors](../details/details_components.md#motor-phase-connectors) and label the wires.<br>On one of the boards we attach a 2 pin Hirose wire to power the Master Board.*<br>

---
## Flashing

The MicroDriver boards are flashed using a JTAG emulator connected via USB.<br> The emulator is connected to the MicroDriver using the connector cable described below.



## Wiring MicroDriver <-> JTAG Emulator

Note: A long wire might cause communication problems when attempting to flash the MicroDriver. A cable length of 10 cm worked well for us.



| Connector Emulator | Connector MicroDriver |
|---|---|
|  |  |

---
## More Information
[Open Dynamic Robot Initiative - Webpage](https://open-dynamic-robot-initiative.github.io)  
[Open Dynamic Robot Initiative - YouTube Channel](https://www.youtube.com/channel/UCx32JW2oIrax47Gjq8zNI-w)  
[Open Dynamic Robot Initiative - Forum](https://odri.discourse.group/categories)  
[Open Dynamic Robot Initiative - Paper](https://arxiv.org/pdf/1910.00093.pdf)  
[Hardware Overview](../../README.md#open-robot-actuator-hardware)  
[Software Overview](https://github.com/open-dynamic-robot-initiative/open-dynamic-robot-initiative.github.io/wiki)

## Authors
* Jonathan Fiene
* Julian Viereck
* Felix Grimminger

## License
BSD 3-Clause License

## Copyright
Copyright (c) 2019-2021, Max Planck Gesellschaft and New York University

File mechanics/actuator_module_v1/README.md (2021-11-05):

# Brushless Actuator Module Core v1



## Description
We developed a light-weight, low cost, minimal complexity, torque-controlled actuator module for robotic research.  
The actuator module consists of a brushless outrunner motor, a high resolution optical encoder, a dual stage timing belt transmission and mostly 3d printed parts and off-the-shelf components.  
The module has a segment length of 160mm, weighs 150g and outputs 2,5Nm at 12A.

The **updated version** of the Brushless Actuator Module Core is documented here: [Actuator Module Core v1.1](actuator_module_v1.1.md#brushless-actuator-module-core-v11)

<br>*Actuator Module Assembly - core components with upper leg shell structure*

## Core Components
<br>
We are using the same core components for all the robots described in this repository. <br> The only difference between the actuator modules is the surrounding shell structure.



We are using a dual stage timing belt transmission with a 3:1 gear reduction on each stage.
The total gear reduction is 9:1.

## Core Component Overview
<br>*Core components - the weight of all the components in the pictures is 95g*

## Off-the-shelf Components

### Brushless DC Motor

 <br>

  * T-Motor Antigravity 4004 300kV
  * 24 magnets / 12 pole pairs / 18 slots
  * 3 phase WYE Configuration / Star Configuration
  * Rotor diameter: 45mm
  * Weight: 53g
  * [Details Motor Preparation](details/details_motor_preparation.md)
  * [Details Motor Shaft Preparation](details/details_motor_shaft_preparation.md)
  * [T-Motor Product Webpage](http://store-en.tmotor.com/goods.php?id=438) (the motors are sold in sets of 2 pieces)
  * [Ordering information below](#bill-of-materials---brushless-actuator-module-core)

### Optical Encoder
 <br>
  * Broadcom AEDT-9810-Z00
  * 5000 pulses per revolution per channel
  * 20000 counts per revolution at the micro controller
  * 5V two channel quadrature output with index pulse (ABZ)
  * Code wheel diameter: 26mm
  * Weight: 5g
  * [Details Encoder and Codewheel](details/details_encoder.md)
  * [Details Encoder Preparation](details/details_encoder_preparation.md)
  * [Details Motor Shaft and Codewheel Preparation](details/details_motor_shaft_preparation.md)
  * [Broadcom Webpage](https://www.broadcom.com/products/motion-control-encoders/incremental-encoders/transmissive-encoders/aedt-981x)  
  * [Ordering information below](#bill-of-materials---brushless-actuator-module-core)

### Timing Belts
 <br> *Timing Belts AT3 GEN III with 50 teeth and 67 teeth - weight: 4,5g*
  * Timing Belt: Conti Synchroflex AT3 GEN III - 3mm tooth pitch
  * Heavy duty polyurethane timing belt with steel cord reinforcements
  * First stage: 150mm timing belt - 50 teeth - width 4mm - 1,5g
  * Second stage: 201mm timing belt - 67 teeth - width 6mm - 3g
  * [Contitech Webpage](https://www.contitech.de/en-gl/Solutions/Power-Transmission/Industrial-Applications/Drive-Belts/Synchronous-Belts/Products/Product-range/CONTI-SYNCHROFLEX-GEN3)  
  * [Ordering information below](#bill-of-materials---brushless-actuator-module-core)

### Bearings
<br>*Stainless steel roller bearings - weight: 16g*
* Miniature EZO stainless steel roller bearings
* Ouput bearing: 32mm x 25mm x 4mm - 6.9g
* Transmission bearing: 8mm x 4mm x 2mm - 0.4g
* Belt tensioner bearing: 7mm x 3mm x 3mm - 0,4g
* [EZO Webpage](https://www.ezo-usa.com/)
* [Ordering information below](#bill-of-materials---brushless-actuator-module-core)

### Fasteners
 <br> *Fasteners Actuator Module Core - weight: 2,9g*

* Fasteners Motor: M3 x 5 Flat Head Screw
* Fasteners Timing Belt Tensioner: M3 x 10 Flat Head Screw
* Washers Timing Belt Tensioner: M2,5 Washer
* Helical Insert Output Shaft: Helicoil M3 x 6
* Fasteners Encoder: M3 x 16 Philipps Flat Head Screw
* [Ordering information below](#bill-of-materials---brushless-actuator-module-core)

## Machined Parts
<br>*Motor shaft, motor pulley and center pulley - weight: 5,9g*

The 3 parts in the picture need to be machined from metal.

  * motor pulley 10 teeth - aluminum - 0.6g -> [PDF drawing](drawings/motor_pulley_at3_t10.PDF)
  * center pulley 10 teeth - aluminum - 2,1g -> [PDF drawing](drawings/center_pulley_at3_t10.PDF)
  * motor shaft - 4mm stainless steel rod - 3,2g -> [PDF drawing](drawings/motor_shaft.PDF)
  * [Details Machined Parts and Technical Drawings](details/details_machined_parts.md)

Alternatively you can order the ODRI Encoder Kit that includes all the machined parts.<br>
More information can be found in the [Actuator Module Core v1.1 Documentation](actuator_module_v1.1.md#brushless-actuator-module-core-v11).  

## 3D Printed Parts

 <br> *3d printed parts - weight of the parts in the picture: 11,3g*

The tooth profile of the pulleys has to be pretty precise and concentric.  
We recommend to print all the parts listed below with a stereolithography or multijet printer.

More information: [Details 3D Printed Parts](details/details_3d_printed_parts.md#details-3d-printed-parts)

All the STL files for 3d printing the parts below can be found here: [STL Files](stl_files) <br>

 <br>

`The recommended printing direction for all the parts below is the positive z direction of the stl files.`

---
 <br>

* Encoder Codewheel PWB Mount - weight: 0,3g<br> [STL file](stl_files/encoder_codewheel_pwb_mount.STL) ([Option A](#bill-of-materials---brushless-actuator-module-core) with Broadcom AEDT-9810-Z00 encoder)  
* Encoder Codewheel Kit Mount - weight: 0,3g<br>[STL file](stl_files/encoder_codewheel_kit_mount.STL) ([Option B](#encoder-and-codewheel---alternative-b) with AEDM-5810-Z12 encoder kit)

  ---
   <br>
* Transmission Pulley AT3 T30 Center - weight 4.2g -> [STL file ](stl_files/transmission_pulley_at3_t30_center.STL)
---
 <br>
* Transmission Pulley AT3 T30 Output - weight 6.7g -> [STL file ](stl_files/transmission_pulley_at3_t30_output.STL)
---
 <br>

* Transmission Belt Tensioner Rollers - weight 0,2g each
* There are STL files with different outer diameters available
* the default diameter that we are using is 10mm
* the different roller diameters allow you to adjust the timing belt tension if required
* 10.0mm Transmission Belt Tensioner Roller -> [STL file](stl_files/transmission_belt_tensioner_roller_10.0mm.STL)
* 10.5mm Transmission Belt Tensioner Roller -> [STL file](stl_files/transmission_belt_tensioner_roller_10.5mm.STL)
* 11.0mm Transmission Belt Tensioner Roller -> [STL file](stl_files/transmission_belt_tensioner_roller_11.0mm.STL)
* 11.5mm Transmission Belt Tensioner Roller -> [STL file](stl_files/transmission_belt_tensioner_roller_11.5mm.STL)
---

## Bill of Materials - Brushless Actuator Module Core


| Description | Quantity | Ordering Information | Comments |  
| --- | :---: | --- | --- |
|T-Motor Antigravity 4004 300kV|1|[T-Motor Store](http://store-en.tmotor.com/goods.php?id=438)<br>[Globeflight # 1974](https://www.globe-flight.de/T-Motor-GF-Antigravity-Set-4004-300KV-2-pcs)|2 motors per set|
|Encoder Broadcom AEDT-9810-Z00|1|[Mouser # 630-AEDT9810Z00](https://www.mouser.com/ProductDetail/Broadcom-Avago/AEDT-9810-Z00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)<br> [DigiKey # 516-3256-ND](https://www.digikey.com/products/en?keywords=516-3256-ND)|Encoder without codewheel|
|Codewheel for Encoder AEDT-9810-Z00|1|[PWB Encoders GmbH # 104768](https://www.pwb-encoders.com/en/encoder-wheels)|Send an email to info@pwb-encoders.com and ask for a quote. PWB ships worldwide. <br> Order number: 104768 / Codewheel with index / 625cpr 3K for AEDT98X / ID 7mm / OD 25,56mm|
|Timing Belt Conti Synchroflex AT3 GEN III<br> width: 4mm / length: 150mm / 50 teeth<br>Timing belt first stage|1|[Reiff # 60047626](https://www.reiff-tpshop.de/shop/de/antriebstechnik/synchroflex-zahnriemen-gen-iii-at3/gen-iii-at3-laenge-150-bis-1011-mm.html)<br> [Beltingonline](https://www.beltingonline.com/at3-gen-iii-synchroflex-timing-belts-4593)<br>|<br> Reiff: The belt with 4mm width is not listed on the Reiff webpage. <br> Send an email to e-services@reiff-gruppe.de and ask for a quote. <br> Reiff ships within Europe.|
|Timing Belt Conti Synchroflex AT3 GEN III<br> width: 6mm / length: 201mm / 67 teeth <br>Timing belt second stage|1|[Reiff # 60005258](https://www.reiff-tpshop.de/shop/de/antriebstechnik/synchroflex-zahnriemen-gen-iii-at3/gen-iii-at3-laenge-150-bis-1011-mm.html) <br> [Beltingonline](https://www.beltingonline.com/at3-gen-iii-synchroflex-timing-belts-4593)|Send an email to e-services@reiff-gruppe.de and ask for a quote.<br>Reiff ships within Europe.|
|Bearing Output Shaft<br>32mm x 25mm x 4mm<br>EZO bearing 61705 2RS VA  |2|[Emiliana Cuscinetti](https://www.emilianacuscinetti.com/en/miniature-bearings/)<br>[Doppiaemme](https://www.doppiaemme.it/en/prodotti/)<br>[EZO USA](https://catalog.ezo-usa.com/category/metric-series-bearings)<br>[SBN](https://www.sbn.de/en/)<br>[Online Bearing Store](https://www.onlinebearingstore.com/6705-2rs-6705-zz-ball-bearings.html)|Italy: [Emiliana Cuscinetti](https://www.emilianacuscinetti.com/en/miniature-bearings/) or [Doppiaemme](https://www.doppiaemme.it/en/prodotti/)<br> USA: [EZO USA](https://catalog.ezo-usa.com/category/metric-series-bearings)<br> All other countries: Send an email to info@sbn.de and ask for a quote - they ship worldwide. <br> SBN # C02748 <br>We use stainless steel bearings.<br>Alternative: Chrome steel bearings from the Online Bearing Store|
|Bearing Motor Shaft and Center Shaft  <br> 8mm x 4mm x 2mm<br>EZO bearing MR84 VA |3|[Emiliana Cuscinetti](https://www.emilianacuscinetti.com/en/miniature-bearings/)<br>[Doppiaemme](https://www.doppiaemme.it/en/prodotti/)<br>[EZO USA](https://catalog.ezo-usa.com/category/metric-series-bearings)<br>[SBN](https://www.sbn.de/en/)<br>[Online Bearing Store](https://www.onlinebearingstore.com/mr84-miniature-ball-bearing-4x8x2-open.html)|Italy: [Emiliana Cuscinetti](https://www.emilianacuscinetti.com/en/miniature-bearings/) or [Doppiaemme](https://www.doppiaemme.it/en/prodotti/)<br> USA: [EZO USA](https://catalog.ezo-usa.com/category/metric-series-bearings)<br> All other countries: Send an email to info@sbn.de and ask for a quote - they ship worldwide.  <br> SBN # N09724 <br>We use stainless steel bearings.<br>Alternative: Chrome steel bearings from the Online Bearing Store|
|Bearing Timing Belt Tensioner<br>7mm x 3mm x 3mm<br>EZO bearing 683 2Z VA<br><br> |2|[Emiliana Cuscinetti](https://www.emilianacuscinetti.com/en/miniature-bearings/)<br>[Doppiaemme](https://www.doppiaemme.it/en/prodotti/)<br>[EZO USA](https://catalog.ezo-usa.com/category/metric-series-bearings)<br>[SBN](https://www.sbn.de/en/)<br>[Online Bearing Store](https://www.onlinebearingstore.com/683-zz-miniature-ball-bearing-id-3-x-od-7x-w-3mm-shielded.html)|Italy: [Emiliana Cuscinetti](https://www.emilianacuscinetti.com/en/miniature-bearings/) or [Doppiaemme](https://www.doppiaemme.it/en/prodotti/)<br> USA: [EZO USA](https://catalog.ezo-usa.com/category/metric-series-bearings)<br> All other countries: Send an email to info@sbn.de and ask for a quote - they ship worldwide. <br>SBN # N05560 <br> We use stainless steel bearings.<br>Alternative: Chrome steel bearings from the Online Bearing Store|
|Encoder Codewheel PWB Mount|1|[STL file](stl_files/encoder_codewheel_pwb_mount.STL)|3d printed part - use SLA, Polyjet or Multijet printer|
|Transmission Pulley AT3 T30 Center|1|[STL file ](stl_files/transmission_pulley_at3_t30_center.STL)|3d printed part - use SLA, Polyjet or Multijet printer|
|Transmission Pulley AT3 T30 Output|1|[STL file ](stl_files/transmission_pulley_at3_t30_output.STL)|3d printed part - use SLA, Polyjet or Multijet printer|
|Timing Belt Tensioner Roller 10mm|2|[STL file](stl_files/transmission_belt_tensioner_roller_10.0mm.STL)<br>|3d printed part - use SLA, Polyjet or Multijet printer|
|Motor Shaft|1|[PDF drawing](drawings/motor_shaft.PDF)|Machined part|
|Motor Pulley|1|[PDF drawing](drawings/motor_pulley_at3_t10.PDF)|Machined part|
|Center Pulley|1| [PDF drawing](drawings/center_pulley_at3_t10.PDF)|Machined part|
|Fasteners Encoder <br> M3 x 16 Philipps Flat Head Screw|2|[Conrad # 839967](https://www.conrad.com/p/toolcraft-839967-countersunk-screws-m3-16-mm-phillips-din-965-plastic-polyamide-10-pcs-839967)|Polyamide plastic<br>10 pieces per set|
|Fasteners Motor<br>M3 x 5 Flat Head Screw |4|[Online Schrauben](https://online-schrauben.de/shop/Schrauben/Innensechskantschrauben/ISO-10642-DIN-7991-Senkschrauben-mit-Innensechskant-aehnl.-DIN-7991/Edelstahl-Rostfrei-A2/M-3-Gewi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)|Stainless Steel<br>Online Schrauben ships within Europe.|
|Fasteners Timing Belt Tensioner<br>M3 x 10 Flat Head Screw|2|[Online Schrauben](https://online-schrauben.de/shop/Schrauben/Innensechskantschrauben/ISO-10642-DIN-7991-Senkschrauben-mit-Innensechskant-aehnl.-DIN-7991/Edelstahl-Rostfrei-A2/M-3-Gewi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)|Stainless Steel<br>Online Schrauben ships within Europe.|
|Washers Timing Belt Tensioner<br>M2,5 Washer|2|[Online Schrauben](https://online-schrauben.de/shop/Scheiben-Federringe/ISO-7092-Unterlegscheiben-fuer-Zylinderkopfschrauben-aehnl.-DIN-433/Edelstahl-Rostfrei-A2-200-HV)|Stainless Steel<br>Online Schrauben ships within Europe.|
|Helical Insert Output Shaft<br> Helicoil M3 x 6|2|[RS # 470-834](https://uk.rs-online.com/web/p/thread-repair-inserts/0470834/)<br>[Hoffmann # 082814 M3](https://www.hoffmann-group.com/GB/en/houk/Power-tools-and-workshop-supplies/Soldering-tools-cleaning-devices-thread-repair/Thread-insert-set%2C-10-or-20-pieces-2×D/p/082814-M3?tId=617)<br>[McMaster # 91732A773](https://www.mcmaster.com/91732A773/)|[M3 Helicoil tools](details/details_tools.md#helicoil-tools) required|

### Encoder and Codewheel - Alternative B
 <br> *Left side: Encoder and codewheel ordered seperately as described above<br>Right side: Alternative B - Encoder Kit - described below*

| Description | Quantity | Ordering Information | Comments |  
| --- | :---: | --- | --- |
|Broadcom Encoder Kit AEDM-5810-Z12|1|[Mouser # 630-AEDM5810Z12](https://www.mouser.de/ProductDetail/Broadcom-Avago/AEDM-5810Z12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)<br>[DigiKey # 516-3253-ND](https://www.digikey.com/product-detail/en/broadcom-limited/AEDM-5810-Z12/516-3253-ND/5357134)|Kit consisting of encoder and codewheel<br>[Instructions Encoder Kit Disassembly](details/details_encoder_kit_disassembly.md#details-encoder-kit-disassembly)|
|Codewheel Mount Encoder Kit|1|[STL file](stl_files/encoder_codewheel_kit_mount.STL)|3d printed part- use SLA, Polyjet or Multijet printer|

### Encoder and Codewheel - Alternative C

<br>*ODRI Encoder Kit Components*<br>

Alternatively you can order the ODRI Encoder Kit that includes all the machined parts, the code wheel and the encoder.<br>
This option is documented here: [Actuator Module Core v1.1 Documentation](actuator_module_v1.1.md#brushless-actuator-module-core-v11).  

### Timing Belt Tensioner - Alternative B

 <br> *Left side: 7mm bearings and 3d printed rollers as described above<br>Right side: Alternative B - 10mm bearings - described below*

| Description | Quantity | Ordering Information | Comments |  
| --- | :---: | --- | --- |
|Bearing Timing Belt Tensioner<br>SKF # 623-2Z<br> 10mm x 3mm x 4mm|2|<br>[RS Germany # 285-0807](https://de.rs-online.com/web/p/kugellager/2850807/)<br>[Quality Bearings Online](https://www.qualitybearingsonline.com/623-2z-skf-miniature-deep-groove-3x10x4mm/?setCurrencyId=2)|Alternative for 7mm x 3mm x 3mm bearing and timing belt tensioner roller above.|
|Fasteners Timing Belt Tensioner<br>M3 x 10 Flat Head  Screw|2|[Online Schrauben](https://online-schrauben.de/shop/Schrauben/Innensechskantschrauben/ISO-10642-DIN-7991-Senkschrauben-mit-Innensechskant-aehnl.-DIN-7991/Edelstahl-Rostfrei-A2/M-3-Gewi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)|Stainless Steel<br>Online Schrauben shipps within Europe.|
|Washers Timing Belt Tensioner<br>M3 Washer|2|[Online Schrauben](https://online-schrauben.de/shop/Scheiben-Federringe/ISO-7092-Unterlegscheiben-fuer-Zylinderkopfschrauben-aehnl.-DIN-433/Edelstahl-Rostfrei-A2-200-HV)<br>[McMaster # 90965A130](https://www.mcmaster.com/90965A130/)|Stainless Steel<br>Online Schrauben shipps within Europe.|

## Details Wires and Connectors

<br>*Connectors Actuator Module*

### Wires and Connectors
| Description | Quantity | Ordering Information | Comments |  
| --- | :---: | --- | --- |
|Motor Phase Connectors 2mm gold<br>Reely RE-1373188|3|[Conrad # 1373188](https://www.conrad.com/p/reely-1373188-battery-plug-2-mm-gold-plated-2-pair-1373188)<br>[HobbyKing](https://hobbyking.com/en_us/2mm-gold-connectors-10-pairs-20pc.html?___store=en_us)|Conrad: 2 pairs per set<br>HobbyKing 10 pairs per set|
|Motor Phase Wires<br>LiY 0.50 mm² black|3|[Kabeltronik # 1601050](https://www.kabeltronik.de/en/electronics-industry/hook-up-wires-stranded/art/hook-up-wire-stranded-extremely-flexible-lify-3/31)<br>[Conrad # 609337](https://www.conrad.com/p/conrad-components-609337-strand-liy-1-x-050-mm-black-25-m-609337)<br>[McMaster # 8054T14](https://www.mcmaster.com/8054t14-8054T184/)|Kabeltronik ships worldwide.<br>100m on spool. <br>The Kabeltronik wires are the most flexible.|
|Encoder Connector<br>Hirose DF13 Socket 5 Pin|1|[RS # 143-015](https://americas.rsdelivers.com/product/hirose/df13-5s-125c/hirose-df13-male-connector-housing-125mm-pitch-5/0143015)<br>[DigiKey # H2182-ND](https://www.digikey.com/products/en?keywords=H2182-ND)|The Hirose DF13 Crimp Tool is required for crimping the wires.<br> [RS # 503-8331](https://americas.rsdelivers.com/product/hirose/df13-tb2630hc/hirose-plier-crimping-tool-for-df13-crimp/5038331)|
|Encoder Connector Crimp Terminals|5|[RS 503-8325](https://americas.rsdelivers.com/product/hirose/df13-2630scf/hirose-df13-female-crimp-terminal-contact-26awg/5038325) <br> [Digi-Key H9992CT-ND](https://www.digikey.com/products/en?keywords=H9992CT-ND)|The Hirose DF13 Crimp Tool is required for crimping the wires.<br> [RS # 503-8331](https://americas.rsdelivers.com/product/hirose/df13-tb2630hc/hirose-plier-crimping-tool-for-df13-crimp/5038331)|
|Encoder Wires<br>LifY 0.14 mm²|5|[Kabeltronik # 1601014](https://www.kabeltronik.de/en/kabeltronik/search/art/hook-up-wire-stranded-extremely-flexible-lify-1/)|Kabeltronik ships worldwide.<br>100m on spool - different colors available.<br> For the encoders we use red, yellow, black, white and green wires.|

### Wiring Convention Encoder
<br>*Wiring Convention Encoder with Kabeltronik Wires*

More wiring information here: [Details Wiring](../../electronics/details/details_wiring.md#details-wiring)

## PDF Drawing
<br>*Actuator Module Overview - Click on picture to view PDF drawing.*

## Step-by-Step Instructions

| Motor Preparation  | Motor Shaft Preparation | Encoder Preparation |Center Pulley Preparation|
| --- | --- | --- | --- |
| |   |   | |

| Output Pulley Preparation | Shell Preparation | Actuator Module Assembly |Actuator Module Testing|
| --- | --- | --- | --- |
| |   |   | |

## More Details
| Details 3d Printed Parts | Details Machined Parts | Mechanical Tools and Consumables |Electronic Components and Tools|
| --- | --- | --- | --- |
|||||

## More Information
[Open Dynamic Robot Initiative - Webpage](https://open-dynamic-robot-initiative.github.io)  
[Open Dynamic Robot Initiative - YouTube Channel](https://www.youtube.com/channel/UCx32JW2oIrax47Gjq8zNI-w)   
[Open Dynamic Robot Initiative - Forum](https://odri.discourse.group/categories)  
[Open Dynamic Robot Initiative - Paper](https://arxiv.org/pdf/1910.00093.pdf)  
[Hardware Overview](../../README.md#open-robot-actuator-hardware)  
[Software Overview](https://github.com/open-dynamic-robot-initiative/open-dynamic-robot-initiative.github.io/wiki)  
[Back to Top of Page](#brushless-actuator-module-core-v1)

## Authors
Felix Grimminger

## License
BSD 3-Clause License

## Copyright
Copyright (c) 2019-2021, Max Planck Gesellschaft and New York University

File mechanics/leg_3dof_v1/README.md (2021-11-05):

# Leg 3dof v1

<br>*Leg 3dof - weight: 485g*<br>

<br>*CAD Model Leg 3dof*  

## Description

* this page describes the 3dof leg that is used for the [Quadruped Robot 12dof](../quadruped_robot_12dof_v1#quadruped-robot-12dof-v1)
* the same actuator modules are also used for the [FingerEdu](../finger_edu_v1/README.md#fingeredu-v1) and the [NYU Finger](../nyu_finger_v1/README.md#nyu-finger-v1)
* the internal components of all the actuator modules are identical: [Core Components](../actuator_module_v1#core-components)

<br>*Submodules: Hip AA, Hip FE, Upper Leg and Lower Leg*

## Core Components

 <br>*Actuator Module Core Components - weight: 95g*<br>

The internal components of the actuator modules are described here:
* [Actuator Module Core v1](../actuator_module_v1/README.md#brushless-actuator-module-core-v1)
* [Actuator Module Core v1.1](../actuator_module_v1/actuator_module_v1.1.md#brushless-actuator-module-core-v11)

## Lower Leg

 <br>*Lower Leg Version v2 and v3 - weight: 22g each*<br>

* the Lower Legs are describes here: [Lower Leg Documentation](../general/lower_legs.md#lower-legs)

## 3D Printed Parts

<br>*3D Printed Parts Leg 3dof - weight: 139g*

 <br>

`The recommended printing direction for all the parts below is the positive z direction of the stl files.`

* The STL files for 3d printing the shells of the 3dof leg can be found here: [STL files 3dof leg](stl_files).
---

<br>
* [Hip AA Module Shell Base - STL file](stl_files/hip_aa_module_shell_base.STL)<br>
* weight: 21g
---
<br>
* [Hip AA Module Shell Cover - STL file](stl_files/hip_aa_module_shell_cover.STL)<br>
* weight: 16g
---
<br>
* [Hip FE Module Shell Base - STL file](stl_files/hip_fe_module_shell_base.STL)<br>
* weight: 25g
---
<br>
* Alternative version of the Hip FE Base shell to simplify the wire routing
* Credit: [Pau Martinez](https://github.com/nitrostormbcn)
* More information: [GitHub Issue - Cable Routing Improving Proposal](https://github.com/open-dynamic-robot-initiative/open_robot_actuator_hardware/issues/38#issuecomment-851453403)
* [Hip FE Module Shell Base Alternative A - STL file](stl_files/hip_fe_module_shell_base_alt_a.STL)<br>
* weight: 26g
---

<br>
* [Hip FE Module Shell Cover - STL file](stl_files/hip_fe_module_shell_cover.STL)<br>
* weight: 16g
---
<br>
* [Upper Leg Module Shell Base - STL file](stl_files/upper_leg_module_shell_base.STL)<br>
* weight: 27g
---
<br>
* [Upper Leg Module Shell Cover - STL file](stl_files/upper_leg_module_shell_cover.STL)<br>
* weight: 15g
---
<br>
* [Lower Leg v2 - STL file](stl_files/lower_leg_v2.STL)<br>
* we print the lower leg on a FDM printer using the "sparse double dense" setting
* alternative Lower Leg Version 3 below
* [Lower Leg Documentation](../general/lower_legs.md#lower-leg-v2)
* weight: 20g
---
 <br>
* [Lower Leg v3 - STL file](stl_files/lower_leg_v3.STL)<br>
* this lower leg is meant for printing as a solid part
* [Lower Leg Documentation](../general/lower_legs.md#lower-leg-v3)
* weight: 20g

## Off-the-shelf Components

### Fasteners

 <br>

* M2,5 and M3 fasteners
* we use stainless steel fasteners

### Helicoil Thread Inserts

 <br>

* we use Helicoil inserts to reinforce the threads of the 3d printed parts
* you need the [Helicoil Tools](../actuator_module_v1/details/details_tools.md#helicoil-tools) to install the threaded inserts
* Helicoil ordering information [below](#bill-of-materials---leg-3dof)

## Bill of Materials - Leg 3dof
<br>

| Description | Quantity | Ordering Information | Comments |  
| --- | --- | --- | --- |
|Core Components|3|[Actuator Module Core v1](../actuator_module_v1/README.md#brushless-actuator-module-core-v1)<br><br>[Actuator Module Core v1.1](../actuator_module_v1/actuator_module_v1.1.md#brushless-actuator-module-core-v11)||  
|Hip AA Module Shell Base |1|[STL file](stl_files/hip_aa_module_shell_base.STL)|[3d printed part](../actuator_module_v1/details/details_3d_printed_parts.md#details-3d-printed-parts)|
|Hip AA Module Shell Cover |1|[STL file](stl_files/hip_aa_module_shell_cover.STL)|[3d printed part](../actuator_module_v1/details/details_3d_printed_parts.md#details-3d-printed-parts)|
|Hip FE Module Shell Base |1|[STL file](stl_files/hip_fe_module_shell_base.STL)|[3d printed part](../actuator_module_v1/details/details_3d_printed_parts.md#details-3d-printed-parts)|
|Hip FE Module Shell Cover |1|[STL file](stl_files/hip_fe_module_shell_cover.STL)|[3d printed part](../actuator_module_v1/details/details_3d_printed_parts.md#details-3d-printed-parts)|
|Upper Leg Module Shell Base |1|[STL file](stl_files/upper_leg_module_shell_base.STL)|[3d printed part](../actuator_module_v1/details/details_3d_printed_parts.md#details-3d-printed-parts)|
|Upper Leg Module Shell Cover |1|[STL file](stl_files/upper_leg_module_shell_cover.STL)|[3d printed part](../actuator_module_v1/details/details_3d_printed_parts.md#details-3d-printed-parts)|
|Lower Leg v2|1|[STL file](stl_files/lower_leg_v2.STL)|[3d printed part](../actuator_module_v1/details/details_3d_printed_parts.md#details-3d-printed-parts)<br>FDM printer setting: sparse double dense|
|Lower Leg v3 |1|[STL file](stl_files/lower_leg_v3.STL)|[3d printed part](../actuator_module_v1/details/details_3d_printed_parts.md#details-3d-printed-parts)<br>Print as a solid part.<br>Alternative for Lower Leg v2|
|Rubber Foot ||Bicycle tire - for example: Schwalbe Lugano 28" 23-622 |Cut 75mm x 7mm segments|
|Fasteners M3x35|2|M3x35 Socket Head Cap Screw|Stainless Steel<br>For Hip AA to Hip FE connection with adapter.|
|Fasteners M3x22|2|M3x22 Socket Head Cap Screw|Stainless Steel<br>For Hip AA to Hip FE connection without adapter.|
|Fasteners M3x16|2|M3x16 Socket Head Cap Screw|Stainless Steel|
|Fasteners M3x12|2|M3x12 Socket Head Cap Screw|Stainless Steel|
|Washer M3|2||Stainless Steel|
|Fasteners M2,5x6|12|M2,5x6 Socket Head Cap Screw|Stainless Steel|
|Fasteners M2,5x10|15|M2,5x10 Socket Head Cap Screw|Stainless Steel|
|Helical Inserts M2,5x3,75|27|Hoffmann 082814 M2,5<br>McMaster 91732A767|M2,5 Helicoil tools required|

## View the 3dof Leg Cad Model in your Web Browser

<br> *Leg 3dof v1 - Click on the picture to view the cad model in your browser*<br>

## Joint Rotation Limiters

<br><br>*Joint Rotation Limiters - weight: 14g each*<br>

* the lower leg and the upper leg can perform multiple rotations
* to prevent multiple rotations and winding up the wires you can install a stopper on the upper leg
* we use silicone tube sections to soften impacts

<br><br>*Comparision Single Stopper and Double Stopper*<br>

* there's an alternative version that also prevents the lower leg from performing multiple rotations
* that version can be installed if a foot-switch is used

All the STL files for 3d printing can be found here: [STL Files Leg 3dof](stl_files)<br>

### 3D Printed Parts

<br>
* [Stopper Upper Leg Base - STL file](stl_files/stopper_upper_leg_base.STL)<br>
* weight: 5g
----

<br>
* [Stopper Upper Leg Cover - STL file](stl_files/stopper_upper_leg_cover.STL)<br>
* weight: 7g

### Bill of Materials - Joint Rotation Limiter

<br>

| Description | Quantity | Ordering Information | Comments |  
| --- | --- | --- | --- |
|Stopper Upper Leg Base|1|[STL file](stl_files/stopper_upper_leg_base.STL)|[3d printed part](../actuator_module_v1/details/details_3d_printed_parts.md#details-3d-printed-parts)|
|Stopper Upper Leg Cover|1|[STL file](stl_files/stopper_upper_leg_cover.STL)|[3d printed part](../actuator_module_v1/details/details_3d_printed_parts.md#details-3d-printed-parts)|
|M2,5x6 Socket Head Cap Screw|1|[Online Schrauben](https://online-schrauben.de/shop/Schrauben/Innensechskantschrauben/ISO-4762-DIN-912-Zylinderkopfschrauben-mit-Innensechskant-aehnl.-DIN-912/Edelstahl-Rostfrei-A2/M-2,5-Gewinde-M-metrisches-Regelgewinde)|Stainless steel.<br>Online Schrauben ships within Europe.|
|M2,5x10 Socket Head Cap Screw|1|[Online Schrauben](https://online-schrauben.de/shop/Schrauben/Innensechskantschrauben/ISO-4762-DIN-912-Zylinderkopfschrauben-mit-Innensechskant-aehnl.-DIN-912/Edelstahl-Rostfrei-A2/M-2,5-Gewinde-M-metrisches-Regelgewinde)|Stainless steel.<br>Online Schrauben ships within Europe.|
|Silicone Tube 10mm Segment|1|O.D. 12mm I.D. 8mm|[Tube Cutter](../actuator_module_v1/details/details_tools.md#tube-cutter)|

## Preparing the 3d Printed Parts

<br>

<br>

<br>

<br>*Joint Rotation Limiter installed on the Upper Leg.*<br>

## More Information
[Open Dynamic Robot Initiative - Webpage](https://open-dynamic-robot-initiative.github.io)  
[Open Dynamic Robot Initiative - YouTube Channel](https://www.youtube.com/channel/UCx32JW2oIrax47Gjq8zNI-w)   
[Open Dynamic Robot Initiative - Forum](https://odri.discourse.group/categories)  
[Open Dynamic Robot Initiative - Paper](https://arxiv.org/pdf/1910.00093.pdf)  
[Hardware Overview](../../README.md#open-robot-actuator-hardware)  
[Software Overview](https://github.com/open-dynamic-robot-initiative/open-dynamic-robot-initiative.github.io/wiki)  

## Authors
Felix Grimminger

## License
BSD 3-Clause License

## Copyright
Copyright (c) 2019-2021, Max Planck Gesellschaft and New York University

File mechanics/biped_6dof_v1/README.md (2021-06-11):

# Biped Robot 6dof v1

 <br>*Biped Robot 6dof  - weight: 1,34kg <br>For this picture the robot was held by a string.*<br><br>

 <br>*Biped Robot CAD model*<br>

## Description

* this page describes all the components that are required to build the Biped Robot
* each leg has 3 active degrees of freedom and a passive ankle joint
* the legs of the Biped Robot are described here: [Biped Leg 3dof v1 Documentation](../biped_leg_3dof_v1/README.md#biped-leg-3dof-v1)
* compared to the quadruped robots the upper and lower leg length  was increased by 25% - from 160mm to 200mm
* since the biped has no leg rotation degree of freedom the yaw angle of the robot cannot be controlled
* the line contact of the feet help to stabilize the yaw orientation of the robot
* the onboard IMU and the Vicon Markers on the body are used for base estimation
* the interface wire provides power and ethernet communication

 <br>*Biped Robot 6dof - front view<br>For this picture the robot was held by a string.*<br>

 <br>*Biped Robot 6dof - back view<br>For this picture the robot was held by a string.*<br>

<br>*Biped Robot 6dof - sitting posture*<br>

## Dimensions

<br>*Biped Robot Dimensons*<br>

<br>*Biped Robot Hip Height - at 45°, 60° and 90° lower leg angle*<br>

## Leg Modules
<br>*Biped Leg Modules - right side and left side - 540g each*<br>

* the legs of the Biped Robot are described here: [Biped Leg 3dof v1 Documentation](../biped_leg_3dof_v1/README.md#biped-leg-3dof-v1)
* all the internal components of the actuator modules are identical
* the internal components of the actuator modules are described here:
  * [Actuator Module Core v1](../actuator_module_v1/README.md#brushless-actuator-module-core-v1)
  * [Actuator Module Core v1.1](../actuator_module_v1/actuator_module_v1.1.md#brushless-actuator-module-core-v11)
* the preparation of the actuator modules is described here:<br>
  * [Step by Step Instructions](../#step-by-step-instructions)

## Body Module
<br>*Biped Body Structure Assembled - weight: 99g*<br>

* the [3d printed parts](#3d-printed-parts) of the body module are listed below
* the [preparation of the 3d printed parts](#preparing-the-3d-printed-parts) is described below

## Electronics

  <br> *Electronic Component Overview*<br>

 <br> *Electronic Components Biped Robot*<br>

### Master Board
 <br> *Master Board v2 - weight: 19g each*<br>
* Custom electronics board: [Master Board Documentation](https://github.com/open-dynamic-robot-initiative/master-board#master-board)

### Micro Driver Boards
 <br> *Micro Driver Boards v2 - stack with 3 cards - weight: 47g*<br>

* Custom electronics board: [Micro Driver Board Documentation](../../electronics/micro_driver_electronics/README.md#micro-driver-electronics)

### Inertia Measurement Unit
<br>

* Lord Microstrain 3DM-CX5-25
* Weight: 13g
* [Lord Microstrain webpage](https://www.microstrain.com/inertial/3dm-cx5-25)
* ordering information [below](#bill-of-materials---biped-robot-6dof)

## 3D Printed Parts

<br>*Parts Body Structure - weight: 87g*

 <br>

`The recommended printing direction for all the parts below is the positive z direction of the stl files.`

All the STL files for 3d printing the body structure can be found here: [STL Files Biped Body Structure](stl_files). <br>

The preparation of the 3d printed parts is described below: [Preparing the 3D Printed Parts](#preparing-the-3d-printed-parts)

More information about 3d printing can be found here: [Details 3D Printed Parts](../actuator_module_v1/details/details_3d_printed_parts.md#details-3d-printed-parts)

---
 <br>
* [Body Structure Front - STL file](stl_files/body_structure_biped_front.STL)<br>
* weight: 19g
---
 <br>
* [Body Structure Back Rev A- STL file](stl_files/body_structure_biped_back_rev_a.STL)<br>
* weight: 14g
---
 <br>
* [Body Structure Right Side - STL file](stl_files/body_structure_biped_right_side.STL)<br>
* weight: 9g
---
 <br>
* [Body Structure Left Side - STL file](stl_files/body_structure_biped_left_side.STL)<br>
* weight: 9g
---
 <br>
* [Body Structure Bottom - STL file](stl_files/body_structure_biped_bottom.STL)<br>
* weight: 17g
---
<br>
* there are 4 different versions of the Body Structure Top element available
* minimal version, with IMU, with Vicon markers and with IMU and Vicon markers

---
 <br>
* [Body Structure Top - STL file](stl_files/body_structure_biped_top.STL)<br>
* weight: 14g
---
 <br>
* [Body Structure Top Vicon - STL file](stl_files/body_structure_biped_top_vicon.STL)<br>
* weight: 15g
---
 <br>
* [Body Structure Top IMU - STL file](stl_files/body_structure_biped_top_imu.STL)<br>
* added IMU attachment to the top structure
* weight: 15g
---
 <br>
* [Body Structure Top IMU Vicon - STL file](stl_files/body_structure_biped_top_imu_vicon.STL)<br>
* added IMU attachment to the top structure
* weight: 16g
---
 <br>
* [Micro Driver Stack Spacer - STL file](stl_files/micro_driver_stack_spacer.STL)<br>
* weight: 0,2g
---
 <br>
* [Stand Attachment - STL file](stl_files/stand_attachment.STL)<br>
* weight: 23g
---
 <br>
* [Master Board Protection - STL file](stl_files/body_structure_master_board_protection.STL)<br>
---

## Off-the-shelf Components
### Hip AA Bearing
 <br>

* Dimensions: 25mm x 20mm x 4mm
* Stainless steel
* Weight: 3,4g each
* Ordering information [below](#bill-of-materials---biped-robot-6dof)

### Fasteners
<br>
* M2, M2,5 and M3 fasteners for the biped robot
* we use stainless steel fasteners
* Ordering information [below](#bill-of-materials---biped-robot-6dof)

<br>
* fasteners for the IMU
* M2,5x16 Slotted Screw - Polyamide Plastic
* Weight: 0,1g each
* Ordering information [below](#bill-of-materials---biped-robot-6dof)

### Helicoil Thread Inserts
<br>
* we use Helicoil inserts to reinforce the threads of the 3d printed parts
* you need the [Helicoil Tools](../actuator_module_v1/details/details_tools.md#helicoil-tools) to install the threaded inserts
* Helicoil ordering information [below](#bill-of-materials---biped-robot-6dof)

### Vicon Markers
 <br>*Reflective markers for motion capture system - weight: 1g each*<br>

* 9.5mm Vicon Markers on the base
* M4 x 10 set screws for a attachment
* Weight: 1g each
* Optional - only required for motion capture system
* Ordering information [below](#bill-of-materials---biped-robot-6dof)

## Bill of Materials - Biped Robot 6dof
<br>

| Description | Quantity | Ordering Information | Comments |  
| --- | --- | --- | --- |
|Biped Leg 3DOF Right Side|1|[Biped Leg 3DOF Documentation](../biped_leg_3dof_v1/README.md#biped-leg-3dof-v1)|Custom assembly|
|Biped Leg 3DOF Left Side|1|[Biped Leg 3DOF Documentation](../biped_leg_3dof_v1/README.md#biped-leg-3dof-v1)|Custom assembly|
| Master Board v2 | 1 | [Master Board Documentation](https://github.com/open-dynamic-robot-initiative/master-board#master-board) | Custom electronics |
| Micro Driver Board v2 | 3 | [Micro Driver Documentation](../../electronics/micro_driver_electronics/README.md#micro-driver-electronics)  | Custom electronics |
|Inertia Measurement Unit| 1 |[Lord Microstrain 3DM-CX5-25](https://www.microstrain.com/inertial/3dm-cx5-25)<br><br> [Distributors](https://www.microstrain.com/support/distributors)| Extended measurement range:<br> Gyro Rate: +/- 900 deg/sec. Accelerometer range: +/- 20G|
|Body Structure Front |1|[STL file](stl_files/body_structure_biped_front.STL)|[3d printed part](../actuator_module_v1/details/details_3d_printed_parts.md#details-3d-printed-parts)|
|Body Structure Back Rev A|1|[STL file](stl_files/body_structure_biped_back_rev_a.STL)|[3d printed part](../actuator_module_v1/details/details_3d_printed_parts.md#details-3d-printed-parts)|
|Body Structure Right Side |1|[STL file](stl_files/body_structure_biped_right_side.STL)|[3d printed part](../actuator_module_v1/details/details_3d_printed_parts.md#details-3d-printed-parts)|
|Body Structure Left Side |1|[STL file](stl_files/body_structure_biped_left_side.STL)|[3d printed part](../actuator_module_v1/details/details_3d_printed_parts.md#details-3d-printed-parts)|
|Body Structure Bottom |1|[STL file](stl_files/body_structure_biped_bottom.STL)|[3d printed part](../actuator_module_v1/details/details_3d_printed_parts.md#details-3d-printed-parts)|
|Body Structure Top |1|[STL file](stl_files/body_structure_biped_top.STL)|[3d printed part](../actuator_module_v1/details/details_3d_printed_parts.md#details-3d-printed-parts)<br>Alternatives below|
|Body Structure Top Vicon |1|[STL file](stl_files/body_structure_biped_top_vicon.STL)|[3d printed part](../actuator_module_v1/details/details_3d_printed_parts.md#details-3d-printed-parts)<br>With Vicon marker attachments|
|Body Structure Top IMU |1|[STL file](stl_files/body_structure_biped_top_imu.STL)|[3d printed part](../actuator_module_v1/details/details_3d_printed_parts.md#details-3d-printed-parts)<br>With IMU attachment|
|Body Structure Top IMU Vicon|1|[STL file](stl_files/body_structure_biped_top_imu_vicon.STL)|[3d printed part](../actuator_module_v1/details/details_3d_printed_parts.md#details-3d-printed-parts)<br>With IMU and Vicon marker attachment|
|Master Board Protection|1|[STL file](stl_files/body_structure_master_board_protection.STL)|[3d printed part](../actuator_module_v1/details/details_3d_printed_parts.md#details-3d-printed-parts)|
|Micro Driver Stack Spacer |8|[STL file](stl_files/micro_driver_stack_spacer.STL)|[3d printed part](../actuator_module_v1/details/details_3d_printed_parts.md#details-3d-printed-parts)|
|Hip AA Bearing<br>25mm x 20mm x 4mm <br> ET2520 2Z VA| 2 | [Emiliana Cuscinetti](https://www.emilianacuscinetti.com/en/miniature-bearings/)<br>[Doppiaemme](https://www.doppiaemme.it/en/prodotti/)<br>[EZO USA](https://catalog.ezo-usa.com/category/metric-series-bearings)<br>[SBN](https://www.sbn.de/en/)|Italy: [Emiliana Cuscinetti](https://www.emilianacuscinetti.com/en/miniature-bearings/) or [Doppiaemme](https://www.doppiaemme.it/en/prodotti/)<br> USA: [EZO USA](https://catalog.ezo-usa.com/category/metric-series-bearings)<br> All other countries: Send an email to info@sbn.de and ask for a quote - they ship worldwide. <br> SBN # C07024 <br>We use stainless steel bearings.|
|Vicon Markers Ø 9,5mm | 8 |[Vicon Distributors](https://www.vicon.com/contact/)|Reflective Vicon Marker, solid, on plastic foot, Ø 9,5mm|
|Fasteners Vicon Markers<br>M4x10 Set Screw | 8 |[Online Schrauben](https://online-schrauben.de/shop/Schrauben/Innensechskantschrauben/DIN-913-Gewindestifte-mit-Innensechskant-und-Kegelkuppe-aehnl.-ISO-4026/Edelstahl-Rostfrei-A2/M-4-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)|Stainless steel.<br>Online Schrauben ships within Europe.|
|Fasteners Body Structure<br>M3x8 Socket Head Cap Screw|18|[Online Schrauben](https://online-schrauben.de/shop/Schrauben/Innensechskantschrauben/ISO-4762-DIN-912-Zylinderkopfschrauben-mit-Innensechskant-aehnl.-DIN-912/Edelstahl-Rostfrei-A2/M-3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)|Stainless steel.<br>Online Schrauben ships within Europe.|
|Fasteners Hip AA Modules<br>M3x8 Socket Head Cap Screw|6|[Online Schrauben](https://online-schrauben.de/shop/Schrauben/Innensechskantschrauben/ISO-4762-DIN-912-Zylinderkopfschrauben-mit-Innensechskant-aehnl.-DIN-912/Edelstahl-Rostfrei-A2/M-3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)|Stainless steel.<br>Online Schrauben ships within Europe.|
|Fasteners Micro Driver Stack<br>M2,5x25 Socket Head Cap Screw|4|[Online Schrauben](https://online-schrauben.de/shop/Schrauben/Innensechskantschrauben/ISO-4762-DIN-912-Zylinderkopfschrauben-mit-Innensechskant-aehnl.-DIN-912/Edelstahl-Rostfrei-A2/M-2,5-Gewinde-M-metrisches-Regelgewinde)|Stainless steel.<br>Online Schrauben ships within Europe.|
|Fasteners Master Board<br>M2x5 Socket Head Cap Screw|2|[Online Schrauben](https://online-schrauben.de/shop/Schrauben/Innensechskantschrauben/ISO-4762-DIN-912-Zylinderkopfschrauben-mit-Innensechskant-aehnl.-DIN-912/Edelstahl-Rostfrei-A2/M-2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)|Stainless steel.<br>Online Schrauben ships within Europe.|
|Fasteners Master Board<br>M2x20 Socket Head Cap Screw|2|[Online Schrauben](https://online-schrauben.de/shop/Schrauben/Innensechskantschrauben/ISO-4762-DIN-912-Zylinderkopfschrauben-mit-Innensechskant-aehnl.-DIN-912/Edelstahl-Rostfrei-A2/M-2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)|Stainless steel.<br>Online Schrauben ships within Europe.|
|Fasteners IMU<br>M2,5x16 Slotted Screw|3|[Conrad 839940-62](https://www.conrad.com/p/toolcraft-839940-allen-screws-m25-16-mm-slot-din-84-iso-1207-plastic-polyamide-10-pcs-839940)|Polyamide Plastic<br>Shorten to 13mm|
|Helicoil M3 x 4,5mm|24|[RS 470-838](https://de.rs-online.com/web/p/reparatur-einsatzgewinde/0470838/)<br>[Hoffmann 082812 M3](https://www.hoffmann-group.com/GB/en/houk/Power-tools-and-workshop-supplies/Soldering-tools-cleaning-devices-thread-repair/Thread-insert-set%2C-10-or-20-pieces-1-5×D/p/082812-M3?tId=438)|1,5xD<br>Böllhoff 41890030045|
|Helicoil M2,5 x 3,75mm|4|[RS 470-856](https://de.rs-online.com/web/p/reparatur-einsatzgewinde/0470856/)<br>[Hoffmann 082812 M2,5](https://www.hoffmann-group.com/GB/en/houk/Power-tools-and-workshop-supplies/Soldering-tools-cleaning-devices-thread-repair/Thread-insert-set%2C-10-or-20-pieces-1-5×D/p/082812-M2%2C5?tId=362)|1,5xD<br>Böllhoff 41890250375|

## Preparing the 3D Printed Parts

<br>

---
<br>

---
<br>

---
<br>

<br>

---
<br>

<br>

## Biped Wiring

### Actuator Module Wiring

<br>*Biped Wiring*<br>

| Description | Wire Length | Comments |  
| --- | --- | --- |
|Hip AA Motor Phases |20cm|RHAA and LHAA |
|Hip AA Encoder Wire |28cm|RHAA and LHAA|
|Hip FE Motor Phases |27cm|RHFE and LHFE |
|Hip FE Encoder Wire |33cm|RHFE and LHFE|
|Knee Motor Phases |35cm|RK and LK |
|Knee Encoder Wire |42cm|RK and LK|

More wiring information: [Details Wiring](../../electronics/details/details_wiring.md#details-wiring)

### Robot Interface Wire
<br>

| Description | Quantity | Wire Length | Comments |  
| --- | --- | --- | --- |
|Ethernet Wire |1|6m|4 conductors<br>[Details Wiring](../../electronics/details/details_wiring.md#details-wiring)|
|Power Wires |2|6m|24V and ground<br>[Details Wiring](../../electronics/details/details_wiring.md#details-wiring)|

### SPI Wires
<br>

| Description | Quantity | Wire Length | Comments |  
| --- | --- | --- | --- |
|SPI Wires |3|10cm|5 conductors<br>[Details Wiring](../../electronics/details/details_wiring.md#details-wiring)|

### IMU Wire
<br>

| Description | Quantity | Wire Length | Comments |  
| --- | --- | --- | --- |
|IMU Wire |1|25cm|4 conductors<br>[Details Wiring](../../electronics/details/details_wiring.md#details-wiring)|

### Micro Driver Stack
<br>

| Description | Quantity | Wire Length | Comments |  
| --- | --- | --- | --- |
|Motor Phase Wires |18|11cm|[Details Wiring](../../electronics/details/details_wiring.md#details-wiring)|

### Micro Driver Stack Motor Assignment
<br>

## Vicon Object
 <br>*Body Structure Top element with Vicon markers - weigth: 23g*<br>

 <br>*Biped body structure with Vicon markers - weight: 106g*

<br>*Vicon marker positions - Click on picture above to view the PDF drawing*<br>

* You can download the Vicon object here: [Biped Vicon Object](details/biped_vicon_object.zip)

## Robot Coordinate System Origin
 <br>

* more information about the conventions that we use for our robots: [Conventions](../general/conventions.md#conventions)

## Inertial Sensor Origin Position
 <br>*IMU position - the IMU is colored red in the screenshot above*

* the IMU is mounted to the top element of the body structure
* the label on the IMU is pointing downwards (see picture below)
* the coordinate systems of the IMU and the Biped Robot have the same orientation - more information here: [Coordinate System Conventions](../general/conventions.md#conventions)
* the offset between the coordinate systems is documented below
* the IMU origin is **not** in the geometrical center of the IMU
* [IMU Technical Drawing - see Page 2](https://s3.amazonaws.com/download.microstrain.com/Drawings/3065-0291-ICD.pdf)

|IMU Origin Position in the<br>Robot Coordinate System| X | Y | Z |  
| --- | --- | --- | --- |
||-0,13mm|-6,35mm|77,40mm|

 <br>

## Simplified 3D Model

<br>*Click on picture above to view the PDF drawing.*<br>

* The simplified STL files for visualization and simulation can be found here: [STL Files Visualization](stl_files_for_visualization)

## Biped Inertia Parameters for Simulation
<br>*Biped Inertia Parameters - Click on picture to view PDF document.*<br>

## Robot Stand
 <br>*Biped Robot 6dof - on stand*<br>

| Description | Quantity | Ordering Information | Comments |  
| --- | --- | --- | --- |
|Stand Attachment|1|[STL file](stl_files/stand_attachment.STL)|[3d printed part](../actuator_module_v1/details/details_3d_printed_parts.md#details-3d-printed-parts)|
|Aluminum Profile Back|1|[Item 7.0.000.09](https://product.item24.de/en/products/product-catalogue/productdetails/products/line-8-construction-profiles-1001042794/profile-8-40x40-e-natural-7000009/)|Size 8 - 40mm x 40mm<br>Length: 70cm|
|Aluminum Profile Top|1|[Item 7.0.000.09](https://product.item24.de/en/products/product-catalogue/productdetails/products/line-8-construction-profiles-1001042794/profile-8-40x40-e-natural-7000009/)|Size 8 - 40mm x 40mm<br>Length: 25cm<br>Tap M8x1,25|
|Aluminum Profile Bottom|1|[Item 7.0.000.09](https://product.item24.de/en/products/product-catalogue/productdetails/products/line-8-construction-profiles-1001042794/profile-8-40x40-e-natural-7000009/)|Size 8 - 40mm x 40mm<br>Length: 30cm|
|Aluminum Profile Side|1|[Item 7.0.000.09](https://product.item24.de/en/products/product-catalogue/productdetails/products/line-8-construction-profiles-1001042794/profile-8-40x40-e-natural-7000009/)|Size 8 - 40mm x 40mm<br>Length: 45cm|
|Angle Bracket|4|[Item 0.0.411.15](https://product.item24.de/en/products/product-catalogue/productdetails/products/angle-brackets-zn-1001046547/angle-bracket-set-8-40x40-41115/)|90 degree angle bracket 40mm|
|End Caps|4|[Item 0.0.026.01](https://product.item24.de/en/products/product-catalogue/productdetails/products/caps-for-profiles-in-modular-dimensions-1001042804/cap-8-40x40-black-2601/)|Size 8|
|Rubber Feet|3|[RS 173-5948](https://de.rs-online.com/web/p/dampfungspads/1735948/)|20,6mm x 20,6mm x 7,6mm	|
|Helicoil M4 x 6mm|1|[RS 471-005](https://de.rs-online.com/web/p/reparatur-einsatzgewinde/0471005/)|1,5xD <br>Böllhoff 41890040006<br>M4 Helicoil Tools required.|
|Fastener Stand Attachment<br>M8x25 Flat Head Screw|1|[Online Schrauben](https://online-schrauben.de/shop/Schrauben/Innensechskantschrauben/ISO-10642-DIN-7991-Senkschrauben-mit-Innensechskant-aehnl.-DIN-7991/Edelstahl-Rostfrei-A2/M-8-Gewi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)|Stainless steel.<br>Online Schrauben ships within Europe.|
|Fastener Stand Interface<br>M4x40 Socket Head Cap Screw|1|[Online Schrauben](https://online-schrauben.de/shop/Schrauben/Innensechskantschrauben/ISO-4762-DIN-912-Zylinderkopfschrauben-mit-Innensechskant-aehnl.-DIN-912/Edelstahl-Rostfrei-A2/M-4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)|Stainless steel.<br>Online Schrauben ships within Europe.|
|Fastener Stand Interface<br>M4 Locknut|1|[Online Schrauben](https://online-schrauben.de/shop/Muttern/Sicherungsmuttern/ISO-10511-Sechskantmuttern-selbstsichernd-mit-Polyamid-Klemmteil-Temperaturbereich-50-bis-120-,-gemaess-neuer-ISO-Norm-aehnl.-DIN-985/Edelstahl-Rostfrei-A2)|Stainless steel.<br>Online Schrauben ships within Europe.|

## Robot Stand Preparation
<br>

<br>*Adjust the distance between the screw head and the 3d printed part to about 6,3mm and tighten the lock nut.*<br>

<br>*Tap a M8x1,25 thread into the center hole of the top profile.<br>Install the Stand Attachment with a M8x25 Flat Head Screw.*<br>

<br>*Body Structure Back on Stand Attachment.*<br>

## Robot Calibration

<br>

* [Details Biped Calibration Tool](../general/robot_calibration.md#calibration-tool-biped-6dof)

## View the biped cad model in your web browser
<br>

<br> *Biped Robot 6dof - Click on the picture to view the biped cad model in your browser*<br>

## CAD Files

The Solidworks CAD files are available here: [Biped 6dof v1 Solidworks CAD files](cad_files/Solidworks/biped_6dof_v1.zip)

## Authors
Felix Grimminger

## License
BSD 3-Clause License

## Copyright
Copyright (c) 2019-2021, Max Planck Gesellschaft and New York University

## More Information
[Open Dynamic Robot Initiative - Webpage](https://open-dynamic-robot-initiative.github.io)  
[Open Dynamic Robot Initiative - YouTube Channel](https://www.youtube.com/channel/UCx32JW2oIrax47Gjq8zNI-w)   
[Open Dynamic Robot Initiative - Forum](https://odri.discourse.group/categories)  
[Open Dynamic Robot Initiative - Paper](https://arxiv.org/pdf/1910.00093.pdf)  
[Hardware Overview](../../README.md#open-robot-actuator-hardware)  
[Software Overview](https://github.com/open-dynamic-robot-initiative/open-dynamic-robot-initiative.github.io/wiki)

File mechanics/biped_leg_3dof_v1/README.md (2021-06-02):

# Biped Leg 3dof v1
<br>*Biped Leg 3dof Right Side Cad Model*<br>

<br>*Biped Legs 3dof  - weight: 540g each*<br>

## Description

<br>

This page describes the legs that are used for the [Biped Robot 6dof](../biped_6dof_v1/README.md#biped-robot-6dof-v1). Each leg has 3 torque-controlled degrees of freedom and a passive ankle joint.
The [Hip Actuator Modules](#biped-hip-modules) were modified to reduce the length.
There is a right side and left side version for both hip actuator modules - they are mirrored versions of each other. The length of the [Upper Leg](#upper-leg-module) and the [Lower Leg](#lower-leg-with-passive-ankle-joint) was increased from 160mm to 200mm.

* the internal components of the actuator modules are described here:
  * [Actuator Module Core v1](../actuator_module_v1/README.md#brushless-actuator-module-core-v1)
  * [Actuator Module Core v1.1](../actuator_module_v1/actuator_module_v1.1.md#brushless-actuator-module-core-v11)
* the preparation of the actuator modules is described here:<br>
  * [Step by Step Instructions](../#step-by-step-instructions)

<br>

## Biped Hip Modules

<br>*Biped Hip FE and Hip AA Modules* <br>

* the timing belt of the second stage of the biped hip modules was rotated by 145 degrees
* this makes the modules shorter and more suitable for the biped robot
* only the shell structure was modified - all the internal parts of the actuator modules are identical
* a comparison between the Quadruped Hip FE module and the Biped Hip FE module is shown below

<br>*Comparison Quadruped Hip FE module (top) and Biped Hip FE module (bottom)* <br>

## Hip FE Actuator Module

<br>*Biped Hip FE Actuator Module - weight: 155g* <br>

<br>*Biped Hip FE Actuator Modules - shell covers removed* <br>

<br>*Cad Model Hip FE Actuator Modules - right side version and left side version*

## Hip AA Actuator Module
<br>*Biped Hip AA Actuator Module - weight: 153g* <br>

<br>*Biped Hip AA Actuator Modules - shell covers removed* <br>

<br>*Cad Model Hip AA Actuator Modules - right side version and left side version*<br>

## Upper Leg Module
 <br>*Extended upper leg module for biped robot - weight: 170g* <br>

 <br>*Extended upper leg module - shell cover removed* <br>

 <br>
* initially we were using the standard quadruped upper leg module with a segment length of 160mm for the biped robot
* we are now using an extended upper leg structure with 200mm segment length
* the lower leg length was also increased to 200mm
* the longer legs help to decrease the natural frequency of the system
* the mechanical interfaces of both versions are compatible and all the internal parts are identical

 <br>*Comparison Upper Leg Versions<br>Top: Upper Leg Quadruped Robots / Bottom: Upper Leg Biped Robot* <br>

## Lower Leg with Passive Ankle Joint

 <br>*Foot with passive ankle joint* <br>

* the length of the lower leg was increased to 200mm and a foot with passive ankle joint was added
* the line contact of the new foot helps to stabilize yaw angle of the robot

 <br>*Biped Lower Legs - printed on Fortus printer.<br>Bottom: with carbon fiber reinforcement on both sides.* <br>

* during experiments with the biped robot we found that the lower legs from our Fortus FDM printer with sparse infill are too flexible in the lateral direction
* we recommend to reinforce the lower legs with glass or carbon fibers on the top and bottom side
* alternatively you can 3d print the lower legs on a [Markforged printer](https://markforged.com/3d-printers/onyx-pro) with internal fiber glass reinforcement

 <br>*Biped Lower Leg - printed on Onyx Pro Markforged printer with internal fiber reinforcement - weight: 60g* <br>

## Core Components

 <br>Actuator Module Core Components - weight: 95g

The internal components of the actuator modules are described here:
* [Actuator Module Core v1](../actuator_module_v1/README.md#brushless-actuator-module-core-v1)
* [Actuator Module Core v1.1](../actuator_module_v1/actuator_module_v1.1.md#brushless-actuator-module-core-v11)

## Off-the-shelf Components
 <br>

* Steel pin - diameter 5mm  / length 28mm
* Silicone tube - O.D. 12mm / I.D. 8mm / RS 163-9362
* 4 silicone tube pieces - 2 x 25mm length and 2 x 8mm length
* M2,5 x 20mm socket head cap screw with washers and locknut
* Rubber band

## 3D Printed Parts

<br>*3d printed parts for two biped legs*<br>

 <br>

`The recommended printing direction for all the parts below is the positive z direction of the stl files.`  

All the STL files for 3d printing the biped legs can be found here: [STL Files Biped Leg 3dof](stl_files). <br>

---
 <br>
* [Hip AA Structure Right Side Base - STL file](stl_files/hip_aa_structure_right_side_base.STL)<br>
* print on FDM or SLS printer
* weight: 22g
---
 <br>
* [Hip AA Structure Right Side Cover - STL file](stl_files/hip_aa_structure_right_side_cover.STL)<br>
* print on FDM or SLS printer
* weight: 17g
---
 <br>
* [Hip AA Structure Left Side Base - STL file](stl_files/hip_aa_structure_left_side_base.STL)<br>
* print on FDM or SLS printer
* weight: 22g
---
 <br>
* [Hip AA Structure Left Side Cover - STL file](stl_files/hip_aa_structure_left_side_cover.STL)<br>
* print on FDM or SLS printer
* weight: 17g
---
 <br>
* [Hip FE Structure Right Side Base - STL file](stl_files/hip_fe_structure_right_side_base.STL)<br>
* print on FDM or SLS printer
* weight: 24g
---
 <br>
* [Hip FE Structure Right Side Cover - STL file](stl_files/hip_fe_structure_right_side_cover.STL)<br>
* print on FDM or SLS printer
* weight: 16g
---
 <br>
* [Hip FE Structure Left Side Base - STL file](stl_files/hip_fe_structure_left_side_base.STL)<br>
* print on FDM or SLS printer
* weight: 24g
---
 <br>
* [Hip FE Structure Left Side Cover - STL file](stl_files/hip_fe_structure_left_side_cover.STL)<br>
* print on FDM or SLS printer
* weight: 16g
---
 <br>
* [Upper Leg Structure Base 200mm Rev A - STL file](stl_files/upper_leg_structure_base_200mm_rev_a.STL)<br>
* print on FDM or SLS printer
* weight: 35g
---
 <br>
* [Upper Leg Structure Cover 200mm Rev A - STL file](stl_files/upper_leg_structure_cover_200mm_rev_a.STL)<br>
* print on FDM or SLS printer
* weight: 15g
---
 <br>
* [Lower Leg Structure 200mm - STL file](stl_files/lower_leg_structure_200mm.STL)<br>
* reinforce with glass or carbon fiber on both sides when printing the lower legs on a FDM printer with sparse infill
* alternatively the lower legs can be printed on a [Markforged printer](https://markforged.com/3d-printers/onyx-pro) with internal fiber reinforcement
* weight without fiber reinforcement: 28g
* weight with fiber reinforcement: 32g
---
 <br>
* [Foot Structure - STL file](stl_files/foot_structure.STL)<br>
* print on FDM or SLS printer
* weight: 12g

## Bill of Materials - Biped Legs 3dof v1
<br>*Bill of materials for **two legs** - left side version and right side version.*<br>

| Description | Quantity | Ordering Information | Comments |  
| --- | --- | --- | --- |
|Actuator Module Core Components|6|[Actuator Module Core v1](../actuator_module_v1/README.md#brushless-actuator-module-core-v1)<br><br>[Actuator Module Core v1.1](../actuator_module_v1/actuator_module_v1.1.md#brushless-actuator-module-core-v11)||
|Hip AA Structure Right Side Base|1|[STL file](stl_files/hip_aa_structure_right_side_base.STL)|3d printed part<br>FDM or SLS printer|
|Hip AA Structure Right Side Cover|1|[STL file](stl_files/hip_aa_structure_right_side_cover.STL)|3d printed part<br>FDM or SLS printer|
|Hip AA Structure Left Side Base|1|[STL file](stl_files/hip_aa_structure_left_side_base.STL)|3d printed part<br>FDM or SLS printer|
|Hip AA Structure Left Side Cover|1|[STL file](stl_files/hip_aa_structure_left_side_cover.STL)|3d printed part<br>FDM or SLS printer|
|Hip FE Structure Right Side Base|1|[STL file](stl_files/hip_fe_structure_right_side_base.STL)|3d printed part<br>FDM or SLS printer|
|Hip FE Structure Right Side Cover|1|[STL file](stl_files/hip_fe_structure_right_side_cover.STL)|3d printed part<br>FDM or SLS printer|
|Hip FE Structure Left Side Base|1|[STL file](stl_files/hip_fe_structure_left_side_base.STL)|3d printed part<br>FDM or SLS printer|
|Hip FE Structure Left Side Cover|1|[STL file](stl_files/hip_fe_structure_left_side_cover.STL)|3d printed part<br>FDM or SLS printer|
|Upper Leg Structure Base 200mm Rev A|2|[STL file](stl_files/upper_leg_structure_base_200mm_rev_a.STL)|3d printed part<br>FDM or SLS printer|
|Upper Leg Structure Cover 200mm Rev A|2|[STL file](stl_files/upper_leg_structure_cover_200mm_rev_a.STL)|3d printed part<br>FDM or SLS printer|
|Lower Leg Structure 200mm|2|[STL file](stl_files/lower_leg_structure_200mm.STL)|3d printed part<br>Use FDM printer and reinforce with fibers or use Markforged printer.|
|Foot Structure|2|[STL file](stl_files/foot_structure.STL)|3d printed part<br>FDM or SLS printer|
|Helicoils M3 x 4,5|4|[Ordering Information](../actuator_module_v1/details/details_tools.md#helicoils)|Hip FE Interface|
|Helicoils M2,5 x 3,75|48|[Ordering Information](../actuator_module_v1/details/details_tools.md#helicoils)|Actuator Shells|
|Fasteners M2,5 x 6|34||Actuator Shells|
|Fasteners M2,5 x 10|14||Actuator Shells|
|Fasteners M3 x 22|4||Hip AA Interface|
|Washers M3|4||Hip AA Interface|
|Fasteners M3 x 16|4||Hip FE Interface|
|Fasteners M3 x 12|4||Knee Interface|
|Steel pin 5mm x 28mm|2||Passive Ankle Joint|
|Silicone tube|8|[RS 163-9362](https://uk.rs-online.com/web/p/process-tubing/1639362)|O.D. 12mm / I.D. 8mm <br>4 x 25mm length<br>4 x 8mm length|
|Fastener M2,5 x 20mm|2|||
|Washer M2,5|4|||
|Locknut M2,5|2|||
|Rubber band|2|||

## Actuator Module Wiring
<br>*Biped Wiring*

| Description | Wire Length | Comments |  
| --- | --- | --- |
|Hip AA Motor Phases |20cm|RHAA and LHAA |
|Hip AA Encoder Wire |28cm|RHAA and LHAA|
|Hip FE Motor Phases |27cm|RHFE and LHFE |
|Hip FE Encoder Wire |33cm|RHFE and LHFE|
|Knee Motor Phases |35cm|RK and LK |
|Knee Encoder Wire |42cm|RK and LK|

* More wiring information: [Details Wiring](../../electronics/details/details_wiring.md#details-wiring)

## View the Biped Leg Cad Model in your Web Browser
<br>

<br> *Biped Leg 3dof Right Side<br>Click on the picture to view the biped leg cad model in your browser*

## More Information
[Open Dynamic Robot Initiative - Webpage](https://open-dynamic-robot-initiative.github.io)  
[Open Dynamic Robot Initiative - YouTube Channel](https://www.youtube.com/channel/UCx32JW2oIrax47Gjq8zNI-w)   
[Open Dynamic Robot Initiative - Forum](https://odri.discourse.group/categories)  
[Open Dynamic Robot Initiative - Paper](https://arxiv.org/pdf/1910.00093.pdf)  
[Hardware Overview](../../README.md#open-robot-actuator-hardware)  
[Software Overview](https://github.com/open-dynamic-robot-initiative/open-dynamic-robot-initiative.github.io/wiki)  

## Authors
Felix Grimminger

## License
BSD 3-Clause License

## Copyright
Copyright (c) 2019-2021, Max Planck Gesellschaft and New York University

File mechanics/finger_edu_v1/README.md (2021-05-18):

# FingerEdu v1

 <br>
*Finger module assembled. Weight: 930g*<br>  
 <br>
*The finger can be completely retracted into the base structure for  transport.*<br>  

## Description

 <br>
*Finger Edu - Joint Labels*<br>  

## Actuator Modules
 <br>
*Each finger consists of 3 different actuator modules*<br>  

For the finger we are using the same actuator modules that are used for the 12dof quadruped legs.<br> There is more detailed information here: [Leg 3dof](../leg_3dof_v1)
* Hip AA actuator module - 148g
* Hip FE actuator module - 160g
* Upper Leg actuator module - 155g

## Finger Base Frame
 <br>
*Assembled base frame - weight: 226g*<br>

The STL files for 3d printing the finger base frame can be found here: [STL files](stl_files)

## Finger Link
<br>*Finger link with finger tip - weight: 22g*

The finger link was printed on a FDM printer with the setting: "sparse double dense".  
The STL file for 3d printing the finger link can be found here: [STL files](stl_files)

 <br>*Rubber finger tip - weight 2g*<br>
* we ordered the rubber finger tip from Amazon
* it's a standard office product for handling paper
* look for "Rubber Thimblette" - size 2 - large

## Electronics
 <br>*Texas Instruments dual motor driver stack*<br>

Since space and weight isn't a concern here we are using the [Texas Instruments evaluation motor driver electronics](../../electronics/ti_electronics/README.md).<br>
Each finger module requires 24V power supply and 2 CAN communication channels.

 <br>
*Finger Edu - Motor Driver Card Assignment*<br>  

## 3D Printed Parts

 <br>

`The recommended printing direction for all the parts below is the positive z direction of the stl files.`

* All the STL files for 3d printing the frame and the finger tip can be found here: [STL Files Frame Structure](stl_files) <br>

* All the STL files for 3d printing the actuator shells can be found here: [STL Files Actuator Module Shells](../leg_3dof_v1/stl_files) <br>

---
 <br>
* [Finger Adapter - STL file](stl_files/finger_adapter.STL)<br>
* weight: 10g
---
 <br>
* [Finger Tip - STL file](stl_files/finger_tip.STL)<br>
* weight: 20g
---
 <br>
* [Structure Bottom Plate - STL file](stl_files/structure_bottom_plate.STL)<br>
* weight: 16g
---
 <br>
* [Structure Front Plate - STL file](stl_files/structure_front_plate.STL)<br>
* weight: 23g
---
 <br>
* [Structure Side Plate Left- STL file](stl_files/structure_side_plate_left.STL)<br>
* weight: 100g
---
 <br>
* [Structure Side Plate Right- STL file](stl_files/structure_side_plate_right.STL)<br>
* weight: 71g
---
 <br>
* [TI Stack Spacer- STL file](stl_files/ti_stack_spacer.STL)<br>
* weight: 2g
---
 <br>
* [TI Stack Support- STL file](stl_files/ti_stack_support.STL)<br>
* weight: 3g

-------------
## Authors
Felix Grimminger

## License
BSD 3-Clause License

## Copyright
Copyright (c) 2019-2021, Max Planck Gesellschaft and New York University

## More Information
[Open Dynamic Robot Initiative - Webpage](https://open-dynamic-robot-initiative.github.io)  
[Open Dynamic Robot Initiative - YouTube Channel](https://www.youtube.com/channel/UCx32JW2oIrax47Gjq8zNI-w)   
[Open Dynamic Robot Initiative - Forum](https://odri.discourse.group/categories)  
[Open Dynamic Robot Initiative - Paper](https://arxiv.org/pdf/1910.00093.pdf)  
[Hardware Overview](../../README.md#open-robot-actuator-hardware)  
[Software Overview](https://github.com/open-dynamic-robot-initiative/open-dynamic-robot-initiative.github.io/wiki)

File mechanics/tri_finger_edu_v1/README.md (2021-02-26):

# TriFingerEdu v1

<br>*TriFinger Manipulator Platform*

* the manipulator platform has 9 torque-controlled degrees of freedom
* it consists of 3 identical finger modules attached to an aluminum frame structure
* the finger module is describes in detail here: [Finger Module Page.](../finger_edu_v1/README.md)
* the frame an the required components are described below

 <br> *Finger modules assembled - weight: 930g each*  

 <br> *TriFinger Manipulator Platform - picture overlay<br>Picture: Felix Widmaier, Manuel Wüthrich and Shruti Joshi*

## Frame
 <br> *Frame structure - t-slotted aluminum profiles*

* The frame structure consists of aluminum profiles from Item.   
* You will need the following components to build the frame.  

### Aluminum profiles
 <br> *Item Aluminum profile*
* Item aluminum profiles - Size 8 - 40mm x 40mm - Item part number: 0.0.026.33
* Cut the profiles to length according to [this drawing](details/aluminum_profiles.pdf).
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

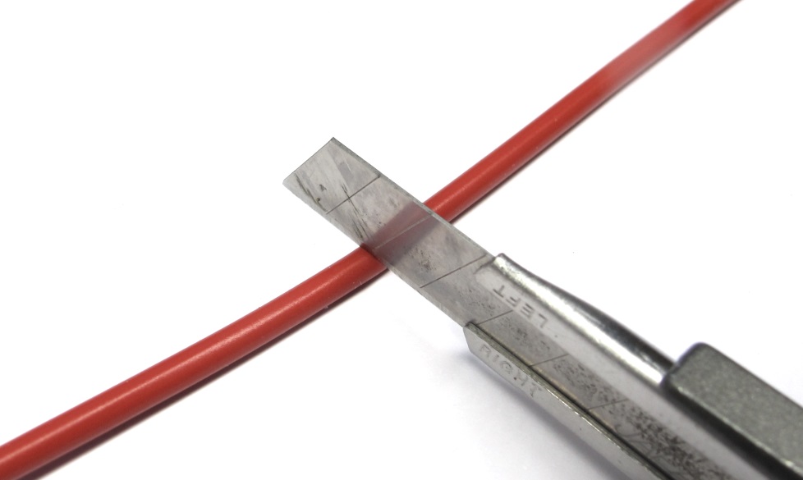
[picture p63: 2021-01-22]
electronics/ti_electronics/images/booster_preparation_15.jpg

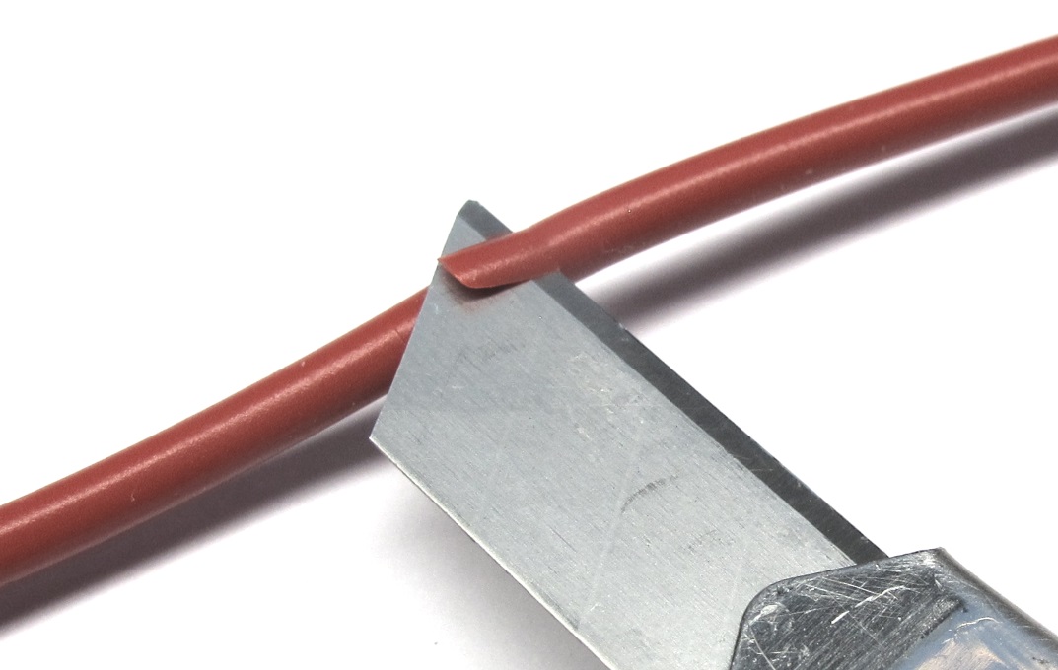
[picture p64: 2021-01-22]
electronics/ti_electronics/images/booster_preparation_17.jpg

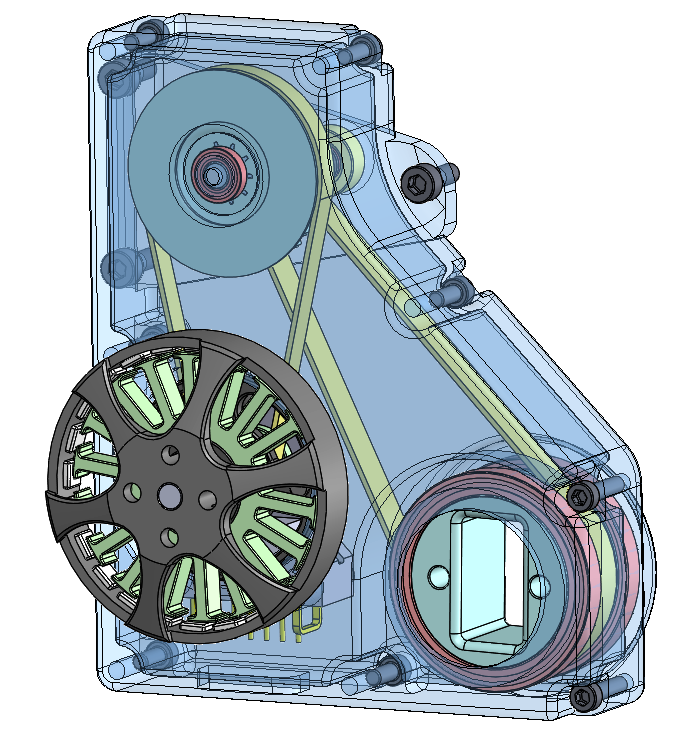
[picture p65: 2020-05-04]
mechanics/biped_leg_3dof_v1/images/biped_hip_aa_module_2.png

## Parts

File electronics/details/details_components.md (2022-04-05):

# Details Electronic Components and Tools

## Hirose DF13 Sockets
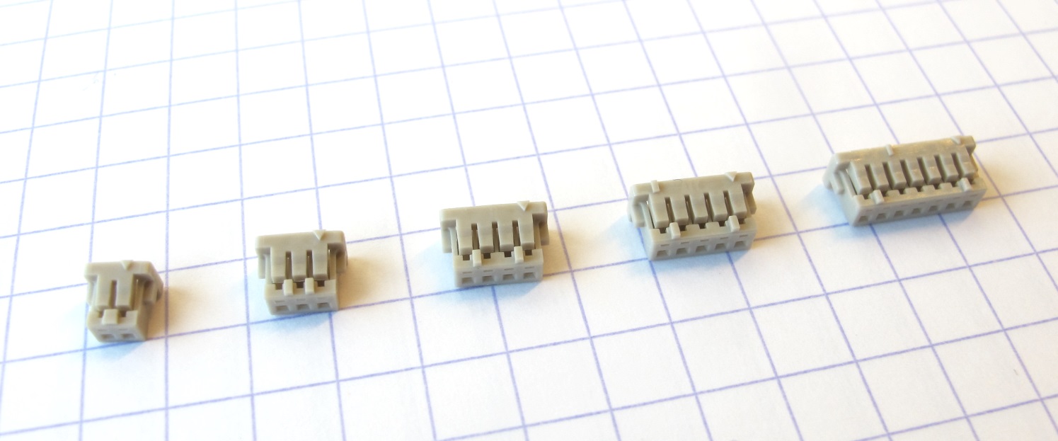
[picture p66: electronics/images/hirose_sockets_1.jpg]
 <br>*Hirose Socket Connectors*

|Description|Details|Ordering Information|Comments|
|---|---|---|---|
|Hirose DF13 Socket 2 Pin|DF13-2S-1.25C|RS 503-7748<br>Digi-Key H2179-ND||
|Hirose DF13 Socket 3 Pin|DF13-3S-1.25C|RS 142-999<br>Digi-Key H2180-ND||
|Hirose DF13 Socket 4 Pin|DF13-4S-1.25C|RS 143-009<br>Digi-Key H2181-ND||
|Hirose DF13 Socket 5 Pin|DF13-5S-1.25C|RS 143-015<br>Digi-Key H2182-ND||
|Hirose DF13 Socket 7 Pin|DF13-7S-1.25C|RS 143-037<br>Digi-Key H2184-ND||  

## Hirose DF13 Straight Pin Headers
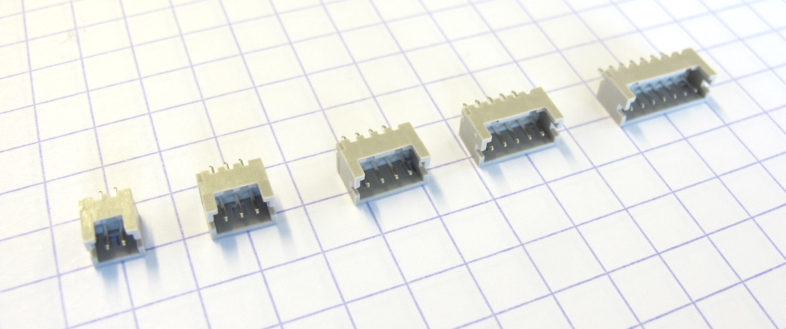
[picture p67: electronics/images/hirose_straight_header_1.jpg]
 <br>*Hirose Straight Pin Headers*

|Description|Details|Ordering Information|Comments|
|---|---|---|---|
|Hirose DF13 Straight Header 2 Pin|DF13-2P-1.25DSA|Digi-Key H2191-ND||
|Hirose DF13 Straight Header 3 Pin|DF13-3P-1.25DSA|Digi-Key H2192-ND||
|Hirose DF13 Straight Header 4 Pin|DF13-4P-1.25DSA|Digi-Key H2193-ND ||
|Hirose DF13 Straight Header 5 Pin|DF13-5P-1.25DSA|Digi-Key H2194-ND||
|Hirose DF13 Straight Header 7 Pin|DF13-7P-1.25DSA|Digi-Key H2196-ND ||

## Hirose DF13 Right Angle Pin Headers
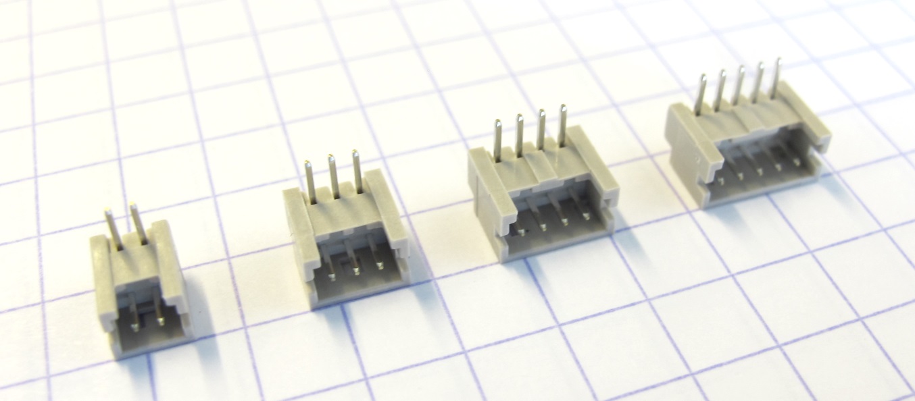
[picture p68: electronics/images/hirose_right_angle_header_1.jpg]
 <br>*Hirose Right Angle Pin Headers*

|Description|Details|Ordering Information|Comments|
|---|---|---|---|
|Hirose DF13 Right Angle Header 2 Pin|DF13-2P-1.25DS(20)|Digi-Key H2199-ND||
|Hirose DF13 Right Angle Header 3 Pin|DF13-3P-1.25DS(20)|Digi-Key H2260-ND||
|Hirose DF13 Right Angle Header 4 Pin|DF13-4P-1.25DS(20)|Digi-Key H2201-ND||
|Hirose DF13 Right Angle Header 5 Pin|DF13-5P-1.25DS(20)|Digi-Key H2202-ND||
|Hirose DF13 Right Angle Header 7 Pin|DF13-7P-1.25DS(20)|Digi-Key H2204-ND||

## Hirose DF13 Crimp Terminals
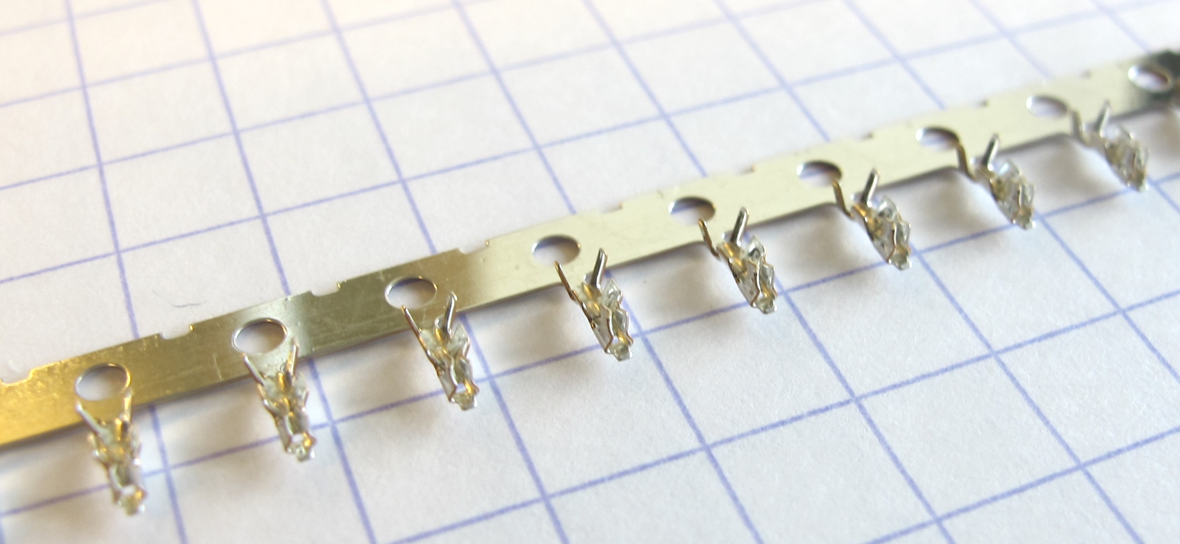
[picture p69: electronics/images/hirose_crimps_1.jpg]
 <br>*Hirose Crimp Terminals*

|Description|Details|Ordering Information|Comments|
|---|---|---|---|
|Crimp Terminal Contact 26-30 AWG<br>Cut tape|DF13-2630SCF|RS 503-8325<br>Digi-Key H9992CT-ND||
|Crimp Terminal Contact 26-30 AWG<br>Reel with 10000 crimp terminals|DF13-2630SCF|Digi-Key H9992TR-ND||

## Hirose Crimp Tool
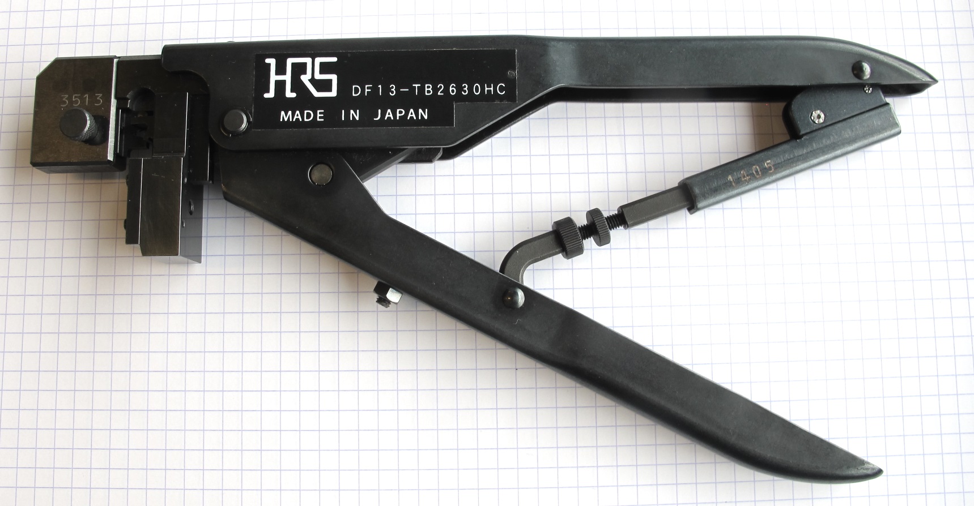
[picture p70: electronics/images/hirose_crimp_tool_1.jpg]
 <br>*Hirose Crimp Tool*

|Description|Details|Ordering Information|Comments|
|---|---|---|---|
|Hirose Crimping Tool for DF13 Crimp Terminals|DF13-TB2630HC|RS 503-8331||

## 30cm Pre-Crimped Hirose Wires
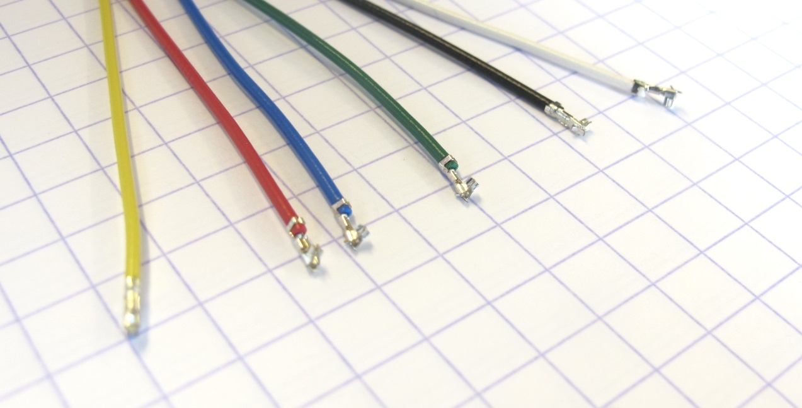
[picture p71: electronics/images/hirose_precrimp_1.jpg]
 <br>*Precrimped Hirose Wires*

|Description|Details|Ordering Information|Comments|
|---|---|---|---|
|30cm pre-crimped DF13 Hirose Wire Red|Pack of 5 wires|RS 180-6028||
|30cm pre-crimped DF13 Hirose Wire Black|Pack of 5 wires|RS 180-6026||
|30cm pre-crimped DF13 Hirose Wire Green|Pack of 5 wires|RS 180-6034||
|30cm pre-crimped DF13 Hirose Wire Yellow|Pack of 5 wires|RS 180-6038||
|30cm pre-crimped DF13 Hirose Wire White|Pack of 5 wires|RS 180-6027||
|30cm pre-crimped DF13 Hirose Wire Blue|Pack of 5 wires|RS 180-6042||

## Power Connectors
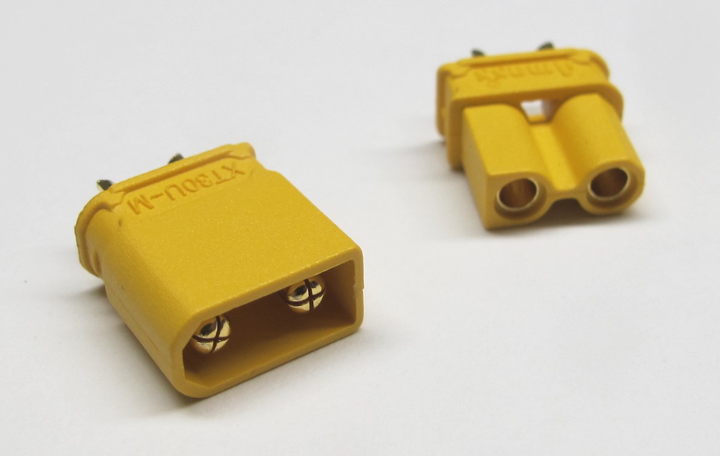
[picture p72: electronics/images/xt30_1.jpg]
 <br>*XT30 Connectors*

|Description|Details|Ordering Information|Comments|
|---|---|---|---|
|XT30U  Connector Receptacle 20 Amps|Reely RE-6619107|Conrad 2206369||
|XT30U Connector Plug 20 Amps|Reely RE-6619104|Conrad 2206368||

## Ethernet Connector
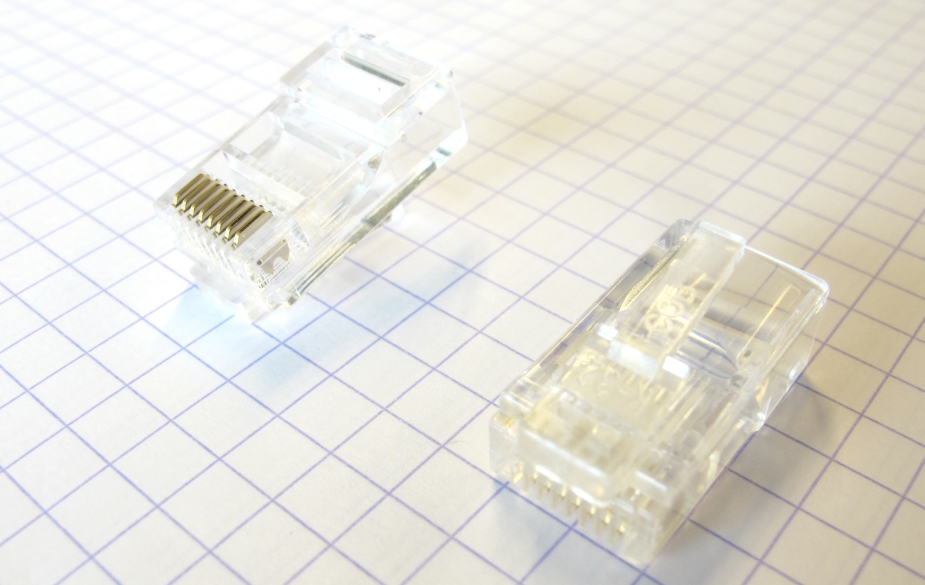
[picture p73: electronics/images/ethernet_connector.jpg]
 <br>*Ethernet Connector*

|Description|Details|Ordering Information|Comments|
|---|---|---|---|
|RJ45 Connector Plug Cat5e|Pack of 5 connectors|RS 821-2949||

## Crimp Tool Ethernet Connector
 <br>*Crimp Tool Ethernet Connector*

|Description|Details|Ordering Information|Comments|
|---|---|---|---|
|Crimping Tool for RJ45 connectors |Paladin|RS 472-6762||

## Ethernet Jack
 <br>*HanRun Ethernet Jack*

|Description|Details|Ordering Information|Comments|
|---|---|---|---|
|Ethernet Jack|HanRun RJ45 HR911105A|[CSD Electronics](https://csd-electronics.de/Mechanical-Comp-/Connectors/Modular/Network/HanRun-RJ45-jack-HR911105A-2xLED::12367.html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)|Used for MasterBoard.|

## Neo Pixel Leds
 <br>*NeoPixel Leds*

|Description|Details|Ordering Information|Comments|
|---|---|---|---|
|Neo Pixel Led|WS2818B LED SMD 5050 with WS2811 controller|Amazon|Used for MasterBoard.|

## Neo Pixel Led Rings
 <br>*NeoPixel Led Rings*

|Description|Details|Ordering Information|Comments|
|---|---|---|---|
|NeoPixel Ring RGB LED 12 x WS2812|Adafruit 1643|Mouser 485-1643 <br>Conrad 1516560||
|Neo Pixel Ring RGB LED 16 x WS2812 |Adafruit 1463|Mouser 485-1463||

## Motor Phase Connectors
 <br>*Motor Phase Connectors*

|Description|Details|Ordering Information|Comments|
|---|---|---|---|
|2mm Gold Connector|Reely RE-1373188<br>2 pairs per pack|Conrad 1373188||

## Motor Phase Wires
 <br>*Motor Phase Wire*

|Description|Details|Ordering Information|Comments|
|---|---|---|---|
|LifY 0,50 mm² black|100m|Kabeltronik 160105009|Highly flexible|
|LiY Wire 0,50 mm² black|25m|Conrad 1567229|Alternative to Kabeltronik wire|

## Kabeltronik Encoder Wires
 <br>*Kabeltronik Encoder Wires*

|Description|Details|Ordering Information|Comments|
|---|---|---|---|
|LifY Cable 0,14 mm² Red|100m| Kabeltronik 160101408||
|LifY Cable 0,14 mm² Blue|100m| Kabeltronik 160101407||
|LifY Cable 0,14 mm² Yellow|100m| Kabeltronik 160101404||
|LifY Cable 0,14 mm² Green|100m| Kabeltronik 160101403||
|LifY Cable 0,14 mm² White|100m| Kabeltronik 160101401||
|LifY Cable 0,14 mm² Black|100m| Kabeltronik 160101409||
|LifY Cable 0,14 mm² Green|100m| Kabeltronik 160101405||
|LifY Cable 0,14 mm² Purple|100m| Kabeltronik 160101410||

## Heat Shrink
 <br>*Heat Shrink Tubing*

|Description|Details|Ordering Information|Comments|
|---|---|---|---|
|Black Heat Shrink Tubing 1.1mm|Alpha Wire FIT-221 / 2:1 Ratio|RS 8395457||
|Black Heat Shrink Tubing 1.5mm|HellermannTyton<br>10m / 3:1 Ratio|RS 448-247||
|Black Heat Shrink Tubing 2.4mm |HellermannTyton<br>10m / 2:1 Ratio|RS 914-6821||
|Black Heat Shrink Tubing 3mm |HellermannTyton<br>10m / 3:1 Ratio|RS 501-4133||
|Black Heat Shrink Tubing 6mm |HellermannTyton<br>5m / 3:1 Ratio|RS 501-4385||
|Black Heat Shrink Tubing 9mm |HellermannTyton<br>5m / 3:1 Ratio|RS 447-399||
|Black Heat Shrink Tubing 12mm |HellermannTyton<br>5m / 3:1 Ratio|RS 501-4111||

## Braided Cable Sleeve
 <br>*Braided Cable Sleeves*

|Description|Details|Ordering Information|Comments|
|---|---|---|---|
|Braided Cable Sleeve 3mm Black|HellermannTyton|RS 187-4600||
|Braided Cable Sleeve 4mm Black|HellermannTyton|RS 187-4616||
|Braided Cable Sleeve 5mm Black|HellermannTyton|RS 187-4622||
|Braided Cable Sleeve 6mm Black|HellermannTyton|RS 187-4638||
|Braided Cable Sleeve 8mm Black|HellermannTyton|RS 187-4644||
|Braided Cable Sleeve 10mm Black|HellermannTyton|RS 187-4650||

## Flashing Connectors
 <br>*Flashing Connectors*

|Description|Details|Ordering Information|Comments|
|---|---|---|---|
|Pin Header 8 Position 1.27mm pitch|Amphenol ICC 20021111-00008T4LF|Digi-Key 609-3711-ND|Flash Cable Micro Driver Side|
|Pin Header 2,54 mm pitch|Assmann AWL254-DG-G72A|RS 674-2347|Flash Cable Flasher Side|

## Ribbon Cable
 <br>*Ribbon Cables*

|Description|Details|Ordering Information|Comments|
|---|---|---|---|
|Ribbon Cable Gray|HARTING 09180107001|DigiKey 1195-4452-ND|Pitch 1,27mm / 0,050" / 10 conductors|
|Ribbon Cable Multicolor|3M 3302-10|DigiKey MC10M-25-ND<br>RS 105-5281|Pitch 1,27mm / 0,050" / 10 conductors|

## IMU Cable
 <br>*Connector for Microstrain IMU*

 <br>*Ribbon Cable for Microstrain IMU*

|Description|Details|Ordering Information|Comments|
|---|---|---|---|
|10 Position Rectangular Connector for Cable Mount|HARWIN M50-3300542|Digi-Key 952-2561-ND<br>RS 909-4391|IMU connector|
|Ribbon Cable|10 conductors - pitch 0,050" /1,27mm - AWG28|Digi-Key AE10G-300-ND|IMU cable|

## Power Connectors and Cable
 <br>*Power Supply Connectors*

 <br>*Power Supply Cable*

|Description|Details|Ordering Information|Comments|
|---|---|---|---|
|Power Connector male 4mm black|Hirschmann 930729100|RS 738-884||
|Power Connector male 4mm red|Hirschmann 930729101|RS 738-890||
|Power Connector female 4mm black|Hirschmann 931804100|RS 175-8974||
|Power Connector female 4mm red|Hirschmann 931804101|RS 175-8980||
|Power Wire 1mm² black|LifY 1mm² - 100m|Kabeltronik 160110009|Highly flexible|
|Power Wire 1mm² red|LifY 1mm² - 100m|Kabeltronik 160110008|Highly flexible|
|Power Wire 1mm² black|Lapp H05V-K 100m|RS 724-4364|Alternative to Kabeltronik wire|
|Power Wire 1mm² red|Lapp H05V-K 100m|RS 724-4361|Alternative to Kabeltronik wire|

## Wire Splice Connectors

 <br>*Wire Splice Connectors*

|Description|Details|Ordering Information|Comments|
|---|---|---|---|
|2 Conductor Wire Splice Connector|Wago 221-412|RS 883-7544|0,2 – 4mm²<br>24 – 12 AWG|
|3 Conductor Wire Splice Connector|Wago 221-413|RS 883-7548|0,2 – 4mm²<br>24 – 12 AWG|
|5 Conductor Wire Splice Connector|Wago 221-415|RS 883-7557|0,2 – 4mm²<br>24 – 12 AWG|

## E-Stop Switch
 <br>*E-Stop Switch*

|Description|Details|Ordering Information|Comments|
|---|---|---|---|
|E-Stop Switch|Schneider Electric Harmony XALK Ø 40mm|RS 330-8587||
|Cable Gland for E-Stop|M20 thread<br>Maximum wire diameter 9mm|RS 669-4660||

## JTAG Flash Programmer
 <br>*JTAG Flash Programmers*

|Description|Details|Ordering Information|Comments|
|---|---|---|---|
|Blackhawk USB100v2 JTAG Emulator|BH-USB-100v2D|[Mouser 716-BH-USB-100V2D](https://eu.mouser.com/ProductDetail/Blackhawk/BH-USB-100v2D?qs=%252B5rE1lKdS9062c1gWyIPPA%3D%3D)<br>[Blackhawk 12139B](https://www.blackhawk-dsp.com/store/12139b.html)||
|JTAG EMULATOR XDS100V2 USB|Spectrum Digital XDS100V2 JTAG|No longer available.||

## Precision Resistors
 <br>*Precision Resistors for Micro Driver Electronics*

|Description|Details|Ordering Information|Comments|
|---|---|---|---|
|Precision Resistors 7mΩ ±1%|CRE2512-FZ-R007E-3|RS 824-0348 |Phase Current Measurement Micro Driver Board|

## Right Angle Pin Headers
 <br>*Right angle pin headers for connecting the motor phase wires*

|Description|Details|Ordering Information|Comments|
|---|---|---|---|
|Right Angle Pin Header|Molex 1 Row Right Angle Pin Header<br>Pitch 2.54mm|RS 360-6364 |Motor Phase Connection Micro Driver Board|

## Power Supply
 <br>*Voltcraft Power Supply*

|Description|Details|Ordering Information|Comments|
|---|---|---|---|
|Lab Power Supply<br>VOLTCRAFT DPPS-32-20|1-32V DC 0-20A 640 W<br>Supply Voltage 230V|Conrad 1086560|20A max.|
|Lab Power Supply<br>VOLTCRAFT DPPS-32-30|1-32V DC 0-30A 960 W<br>Supply Voltage 230V|Conrad 1086563|30A max.|

## CAN Card
 <br>*Dual Channel PCI Express card*

|Description|Details|Ordering Information|Comments|
|---|---|---|---|
|PCAN - PCI Express CAN Card|Dual Channel|PEAK System<br>IPEH-003027|Galvanically isolated|

## CAN Connector
 <br>*9pin D-Sub connector*

|Description|Details|Ordering Information|Comments|
|---|---|---|---|
|9 pin D-Sub Connector||RS 765-9555||

## Heat Shrink Label Maker
 <br>*Rhino Heat Shrink Label Maker*

|Description|Details|Ordering Information|Comments|
|---|---|---|---|
|DYMO Rhino 5200 Heat Shrink Label Maker|DYMO #1755749|RS 686-4702||
|Heat Shrink ø 6mm|DYMO #18051|RS 515-6760|black on white|
|Heat Shrink ø 9mm|DYMO #18053|RS 733-5883|black on white|
|Heat Shrink ø 12mm|DYMO #18055|RS 515-5565|black on white|
|Heat Shrink ø 19mm|DYMO #18057|RS 515-6782|black on white|

## Soldering Iron
 <br>*Soldering iron with temperature control*

|Description|Details|Ordering Information|Comments|
|---|---|---|---|
|Soldering Iron |Ersa i-CON| Conrad 2272879 <br>Farnell 1625358|Temperature Range: 150°C to 450°C|
|Solder|Stannol HS10|RS 518-012|Ø 0.5mm / 250g|

## Heat Gun
 <br>*Heat Gun*<br>

|Description|Details|Ordering Information|Comments|
|---|---|---|---|
|Steinel Heat Gun|Steinel HL Stick| Conrad 818872<br>Farnell 2138307|Temperature not adjustable.|

## Multimeter
 <br>*Multimeter - Fluke 175*

|Description|Details|Ordering Information|Comments|
|---|---|---|---|
|Multimeter|Fluke 175|RS 394-4470<br>Farnell 3558678||

## Test Probes
 <br>*Miniature Test Probes*<br>

|Description|Details|Ordering Information|Comments|
|---|---|---|---|
|Miniature Test Probes|Hirschmann 	932959001|RS 775-681<br>Farnell 1011414||

## Pliers
 <br>*Wire cutter, pliers and wire stripper*

|Description|Details|Ordering Information|Comments|
|---|---|---|---|
|Wire Cutter|Knipex 7732115|Hahn+Kolb 53106040<br>Farnell 3330436||
|Pliers|Knipex 3522115|Hahn+Kolb 53104020<br>Farnell 1715017||
|Wire Stripper|Knipex 1182130|Hahn+Kolb 53110015<br>Farnell 1779811||

## Tweezers
 <br>*Tweezers*<br>

|Description|Details|Ordering Information|Comments|
|---|---|---|---|
|Tweezers|LINDSTRÖM|Hoffmann 727502||

## Third Hand
 <br>*Third hand*<br>

|Description|Details|Ordering Information|Comments|
|---|---|---|---|
|Third Hand||RS 221-7531||

## Batteries and Charging Accessories

 <br>*X-Cube Battery - weight: 68g*<br>

|Description|Details|Ordering Information|Comments|
|---|---|---|---|
|LiPo Battery SLS X-Cube 850mAh |3S1P 11,1V 30C / 60C<br> Dimensions: 60mm x 30mm x 21mm|[SLS Product Page](https://www.stefansliposhop.de/en/batteries/sls-x-cube/sls-x-cube-30c/sls-x-cube-850mah-3s1p-11-1v-30c-60c::1534.html)<br>SLSCUX08503130|The batteries haven't been tested yet - don't use without a power management board!<br>Power connector: XT 30<br>Balancer connector: XH|
|ISDT SMART DUO CHARGER D2|200W, 12A, 2X6S LiPo, Integrated Power Supply|[SLS Product Page](https://www.stefansliposhop.de/en/chargers-power-supplys/isdt/isdt-smart-duo-charger-d2-200w-12a-2x6s-lipo-integrated-power-supply::1916.html)<br>ISDT-D2|Power connector: XT 60<br>Balancer connector: XH|
|BAT-SAFE Safety Case|Inner dimensions: 250 x 165 x 90mm|[SLS Product Page](https://www.stefansliposhop.de/en/lipo-safety-case/bat-safe-safety-case::1841.html)<br>BAT-SAFE||
|Fire Extinguishing Granulate|1L Pillow|[SLS Product Page](https://www.stefansliposhop.de/en/lipo-safety-case/extover-fire-protection-fire-extinguishing-granulate-for-lithium-batteries-pillow-1l::2061.html)<br>EXV-KISS1L||
|Adapter Cable - XT60 to 4mm|Length: 30cm|[SLS Product Page](https://www.stefansliposhop.de/en/chargers-power-supplys/isdt/sls-isdt-adapter-cable-for-charging-cable-with-4mm-banana-plug::1821.html)<br>SLS-ISDT ALK||
|Adapter Cable - XT30 to 4mm|Length: 30cm|[SLS Product Page](https://www.stefansliposhop.de/en/accessories/charge-cable/sls-xt30-charge-cable::1872.html)<br>SLS XT30 Ladekabel||
|XH-XH Balancer Extension Wire|Length: 25cm|[SLS Product Page](https://www.stefansliposhop.de/en/accessories/balancer-cables/sls-sensor-cable-xh-xh-3s-long::1754.html)<br>SLSXHXHL3S| XH female to XH male 3S|

## Switches
 <br>*Push button switches - weight: 3,5g each*<br>

|Description|Details|Ordering Information|Comments|
|---|---|---|---|
|Push Button Switch Red|ø13,6mm<br>Normally closed - momentarily open while pushed |RS 820-7587|E-stop switch for robots|
|Push Button Switch Green|ø13,6mm<br>Normally open - momentarily closed while pushed |RS 820-7593|On-off switch for robots|

## Gamepad - Robot Input Device

 <br>*XBox One Game Pad with Rechargeable Batteries*<br>

|Description|Details|Ordering Information|Comments|
|---|---|---|---|
|XBox One Wireless Controller Gamepad|Microsoft QAT-00002|Conrad 2336905|USB C charging interface|
|XBox Play&Charge Kit|Microsoft SXW-00002|Conrad 2336907|For gamepad with USB C charging interface|

---
## More Information
[Open Dynamic Robot Initiative - Webpage](https://open-dynamic-robot-initiative.github.io)  
[Open Dynamic Robot Initiative - YouTube Channel](https://www.youtube.com/channel/UCx32JW2oIrax47Gjq8zNI-w)   
[Open Dynamic Robot Initiative - Forum](https://odri.discourse.group/categories)  
[Open Dynamic Robot Initiative - Paper](https://arxiv.org/pdf/1910.00093.pdf)  
[Hardware Overview](../../README.md#open-robot-actuator-hardware)  
[Software Overview](https://github.com/open-dynamic-robot-initiative/open-dynamic-robot-initiative.github.io/wiki)  

## Authors
Felix Grimminger

## License
BSD 3-Clause License

## Copyright
Copyright (c) 2019-2021, Max Planck Gesellschaft and New York University

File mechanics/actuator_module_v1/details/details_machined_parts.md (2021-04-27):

# Details Machined Parts

 <br >*Machined parts - motor shaft, motor pulley and center pulley.*<br>

There are 3 parts in the actuator module that have to be machined from metal - there is more information below.

Alternatively you can order the ODRI Encoder Kit that includes all the machined parts. More information can be found in the [Actuator Module Core v1.1 Documentation](../actuator_module_v1.1.md#brushless-actuator-module-core-v11).

## Timing Belt Pulleys

### Description:

For best performance the tooth profile of the pulleys has to be very precise.  
You can order a custom form cutter with the right cutting profile geometry and machine the parts on a milling machine.  
(Option A below)  
Alternatively you can use Wire EDM (Wire Electrical Discharge) machining to generate the 2d tooth profile.  
(Option B below)  
The remaining machining steps can be done on a lathe.   

**Caution: Don't use standard AT3 timing belt pulley dimensions or tools.  
We modified the original AT3 tooth profile in order to reduce backlash.**

### Option A - Form Cutter

 <br >*Custom Form Cutter with AT3 tooth profile*

 <br>*Aluminum AT3 pulleys machined with Custom Form Cutter*

#### Instructions
* Find a company that offers custom tooling and that can produce custom form cutters.  
* Send them this [PDF Drawing](../drawings/pulley_at3_t10_form_cutter.PDF) and ask them to quote a custom form cutter that will create the specified profile.
* You should mention that the tool will be used to machine 7075 aluminum.
* We use a 3mm shaft form cutter with 3 teeth at a helix angle of 20 degrees.
* When you have received your custom form cutter send the tool and the drawings below to a machine shop of your choice and have the parts machined.  
* [Drawing Motor Pulley](../drawings/motor_pulley_at3_t10.PDF)  
* [Drawing Center Pulley](../drawings/center_pulley_at3_t10.PDF)

---
### Option B - Wire EDM Cutting

 <br>

#### Instructions

* alternatively the tooth profile can be generated with a wire edm machine
* we did some initial tests to evaluate this option
* in terms of cost it doesn't seem to be an advantage and we're not sure how the much rougher surface will affect the life span of the timing belts
* we are therefore not pursuing this option any longer
* [PDF Drawing Wire EDM Geometry](../drawings/pulley_at3_t10_wire_edm.PDF)  
* [DXF File Wire EDM Geometry](../drawings/pulley_at3_t10_wire_edm.zip)

---

## Motor Shafts

 <br>

* for the machining the motor shafts we order 4mm h9 precision ground stainless steel stock material
* the stock material diameter is between 3,99mm and 3,97mm
* the stock material fits the motor bearings without additional adjustments
* we order the stock material from [Weinmann Aach](https://weinmann-aach.de/) in Germany
* Precision Ground Stainless Steel Rod 1.4301 EN10278 h9 4,0mm (erd4)
* machine the motor shafts according to this drawing: [PDF Drawing Motor Shaft](../drawings/motor_shaft.PDF)

---
## Step-by-Step Instructions

| Motor Preparation  | Motor Shaft Preparation | Encoder Preparation |Center Pulley Preparation|
| --- | --- | --- | --- |
| |   |   | |

| Output Pulley Preparation | Shell Preparation | Actuator Module Assembly |Actuator Module Testing|
| --- | --- | --- | --- |
| |   |   | |

---
## More Details
| Details 3d Printed Parts | Details Machined Parts | Mechanical Tools and Consumables |Electronic Components and Tools|
| --- | --- | --- | --- |
|||||

---
## More Information
[Open Dynamic Robot Initiative - Webpage](https://open-dynamic-robot-initiative.github.io)  
[Open Dynamic Robot Initiative - YouTube Channel](https://www.youtube.com/channel/UCx32JW2oIrax47Gjq8zNI-w)   
[Open Dynamic Robot Initiative - Forum](https://odri.discourse.group/categories)  
[Open Dynamic Robot Initiative - Paper](https://arxiv.org/pdf/1910.00093.pdf)  
[Hardware Overview](../../../README.md#open-robot-actuator-hardware)  
[Software Overview](https://github.com/open-dynamic-robot-initiative/open-dynamic-robot-initiative.github.io/wiki)  
[Back to Actuator Module](../README.md)  
[Back to Top of Page](#details-machined-parts)

---
## Authors
Felix Grimminger

## License
BSD 3-Clause License

## Copyright
Copyright (c) 2019-2021, Max Planck Gesellschaft and New York University

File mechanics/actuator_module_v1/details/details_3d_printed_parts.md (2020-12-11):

# Details 3D Printed Parts

## Description
* there are two categories of parts for which we use the following different printing technologies for best results.
* for **large structural parts** like the shells and the body structures of the robots we use a **FDM** (Fused Deposition Modeling) printer  or a **SLS** (Selective Laser Sintering) printer.
* for the **small parts** that require **high precision** like the pulleys for the timing belt transmission we use a **Multijet** or **SLA** (Stereolithography) printer.

<br>*Comparison 3d printed parts: Body structure from FDM printer and pulley from Multijet printer.*  

---
## Printing Tolerances

<br>*Shell base and shell cover - the critical surfaces are colored yellow*  

* the printing tolerances vary significantly depending on the supplier, the printing technology and even between orders from the same supplier
* the critical surfaces for the shells are the bearing seats (colored yellow in the screenshot above)
* if the bearing seat diameters are too tight you can use a end mill to adjust the diameter
* if the bearing seat diameters are much too large the bearings will not be held securely and the parts might not be usable
* ideally you can produce the 3d printed parts on your own 3d printer
* that allows you to do test prints and adjust the printer settings or the STL files if necessary
* at MPI in Tübingen we use the following two 3d printers to produce and evaluate the parts for our robots
---
## Printers at MPI Tübingen

### Fortus FDM Printer
<br>*Fortus 360mc FDM Printer. Picture source: Stratasys*

We use the following material and settings:
* Model material: PC-ABS material black
* Support material: SR20
* T12 nozzle for material and support - slice height 0,178mm
* Mechanical removal or alkaline bath removal of the support material
* Standard solid interior printer setting for all the shell and body parts
* Sparse double dense printer setting for the lower legs

<br>*3d printed shell parts on the build sheet - the brown material is the support.*

<br>*Lower leg printed with sparse double dense setting.<br>For the bottom part the printer was stopped half way to reveal the internal structure.*  

### Projet Multijet Printer
<br>*Projet 3500 HD Max Multijet Printer. Picture source: 3D Systems*  

* Model material: VisiJet M3X
* Support material: S300 Wax
* Oven for removing the wax support material
* Ultrasonic bath with baby oil for removing remaining wax
* Ultrasonic bath with soap water for cleaning the parts
* Quenching in ice water

<br>*All the parts that require high precision and detail are printed on our Projet 3d printer.*

<br>*Projet parts on build plate.*

---
## Ordering Shells from 3D Systems
 <br>  

The shells should be printed on a selective laser sintering printer using high strength material.  
The shells we are using were purchased from the ["3D Systems Part on Demand Service".](https://www.3dsystems.com/on-demand-manufacturing)

 <br>  <br>  

### Instructions:
* go to the website and login (or create a user account if you don't have one yet)
* upload the stl files (actuator_shell_base and actuator_shell_cover)
* choose the printing technology: SLS - Selective Laser Sintering
* choose the material: Duraform HST
* choose number of copies
* save the order and write down the order number (don't order online)
* send an email to the 3D Systems engineering support with the order number and ask for a quote for printing the parts with the printing direction in the positive z axis direction of the STL files as shown below
* You can find the email contact for Germany, France and the US below.

 <br>  <br>

**Important:**   
The print orientation of the parts for the actuator module is critical.  
If you order the parts directly from the online system they will be automatically placed in the print volume by an algorithm.  
If the algorithm places the parts under some random angle they might be not usable.  
In order to control the print orientation and therefore the quality of the parts you have to go through the 3D Systems engineering support.   
Write an email (contact information below) with the order number from the web interface and ask them to give you a quote for printing the parts with the printing direction in the positive z-axis direction of the STL files as shown above.

---
## Pulleys and Code Wheel Mount
The pulleys and the code wheel mount should be printed on a high-detail stereolithography or multijet printer.   
We print these parts on our Projet 3500 HD max multijet printer using the M3X material.  

You can also order these parts from ["3D Systems Part on Demand Service".](https://www.3dsystems.com/on-demand-manufacturing)  
Therefore you should choose the SLA Steroelithography printer and the Accura Extreme Grey Material.

* go to the website and login (or create a user account if you don't have one yet)
* upload the stl files (encoder_codewheel_pwb_mount, transmission_pulley_at3_t30_center and transmission_pulley_at3_t30_output)
* choose the printing technology: SLA - Stereolithography
* choose the material: Accura Extreme Grey
* choose number of copies
* save the order and write down the order number (don't order online)
* send an email to the 3D Systems engineering support with the order number and ask for a quote for printing the parts with the printing direction in the positive z-axis direction of the STL files as shown above.
* You can find the email contact for Germany, France and the US below.

 <br>

---
### 3D Systems Engineering Support:
Germany: anfrage@3dsystems.com    / Phone: 06105-3248-456  
France: lydie.caze@3dsystems.com  
US: chris.lewis@3dsystems.com  
Webpage: [3D Systems Part on Demand Service](https://www.3dsystems.com/on-demand-manufacturing)  

---
## Step-by-Step Instructions

| Motor Preparation  | Motor Shaft Preparation | Encoder Preparation |Center Pulley Preparation|
| --- | --- | --- | --- |
| |   |   | |

| Output Pulley Preparation | Shell Preparation | Actuator Module Assembly |Actuator Module Testing|
| --- | --- | --- | --- |
| |   |   | |

---
## More Details
| Details 3d Printed Parts | Details Machined Parts | Mechanical Tools and Consumables |Electronic Components and Tools|
| --- | --- | --- | --- |
|||||

---
## More Information
[Open Dynamic Robot Initiative - Webpage](https://open-dynamic-robot-initiative.github.io)  
[Open Dynamic Robot Initiative - YouTube Channel](https://www.youtube.com/channel/UCx32JW2oIrax47Gjq8zNI-w)   
[Open Dynamic Robot Initiative - Forum](https://odri.discourse.group/categories)  
[Open Dynamic Robot Initiative - Paper](https://arxiv.org/pdf/1910.00093.pdf)  
[Hardware Overview](../../../README.md#open-robot-actuator-hardware)  
[Software Overview](https://github.com/open-dynamic-robot-initiative/open-dynamic-robot-initiative.github.io/wiki)  
[Back to Actuator Module](../README.md)  
[Back to Top of Page](#details-3d-printed-parts)

---
## Authors
Felix Grimminger

## License
BSD 3-Clause License

## Copyright
Copyright (c) 2019-2020, Max Planck Gesellschaft and New York University

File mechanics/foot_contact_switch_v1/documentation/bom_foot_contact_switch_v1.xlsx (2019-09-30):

Bill of Materials for foot_contact_switch_v1.sch, 13.09.2019
Qty | Part | Value | Description | Order code | Part number
2 | CAB1, CAB7 | WIREWRAP_BLACK_AWG30 | Wirewrap cable black 30AWG | Burklin 91F5041 | 370103009
1 | CAB2 | WIREWRAP_GREEN_AWG30 | Wirewrap cable green 30AWG | Burklin 91F502 | 370103003
1 | CAB3 | WIREWRAP_BLUE_AWG30 | Wirewrap cable blue 30AWG | Burklin 91F5045 | 370103007
2 | CAB4, CAB6 | WIREWRAP_RED_AWG30 | Wirewrap cable red 30AWG | Burklin 91F5043 | 370103008
1 | CAB5 | WIREWRAP_YELLOW_AWG30 | Wirewrap cable yellow 30AWG | Burklin 91F500 | 370103004
1 | IC1 | MCP6V261 | SMD OP Amp rail-to-rail | RS 7559568 | MCP6V26-E/MS
2 | LED1, LED3 | HSFM-C155 | SMD dual LED red/green 20mA 2,1V | Farnell 5790888 | HSMF-C155
1 | LED2 | LED_SMD_WHITE_1206 | SMD LED White 20mA 3V | Farnell 2470224 | 158301260
1 | Q1 | ALS-PT19-315C | SMD phototransistor | Digi-Key 1080-1244-1-ND | ALS-PT19-315C/L177/TR8
4 | R1, R2, R6, R7 | S51R_0603 | SMD resistor 51Ohm | Farnell 2614454 | MCT06030C5109FP500
2 | R3, R4 | S10K_0603 | SMD resistor 10kOhm | Farnell 2613718 | RN73C1J10KBTDF
1 | R5 | S20K_0603 | SMD resistor 20kOhm | Farnell 1469774 | CRCW060320K0FKEA
1 | R8 | S560R_0603 | SMD resistor 560Ohm | Farnell 2502470 | WR06X5600FTL

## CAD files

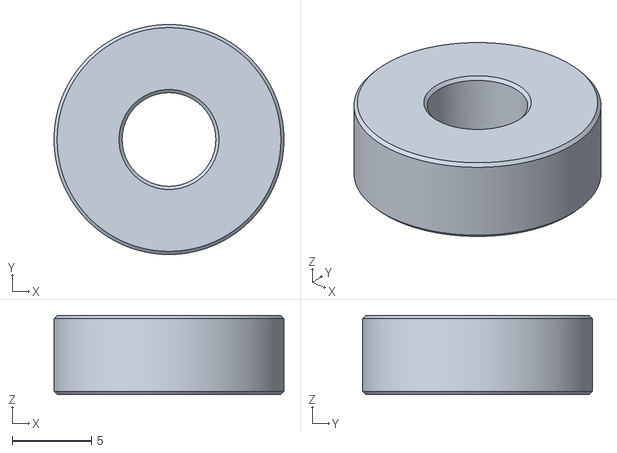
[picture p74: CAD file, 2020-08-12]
mechanics/actuator_module_v1/stl_files/tool_center_pulley_assembly.STL
14.5 x 14.5 x 5.00

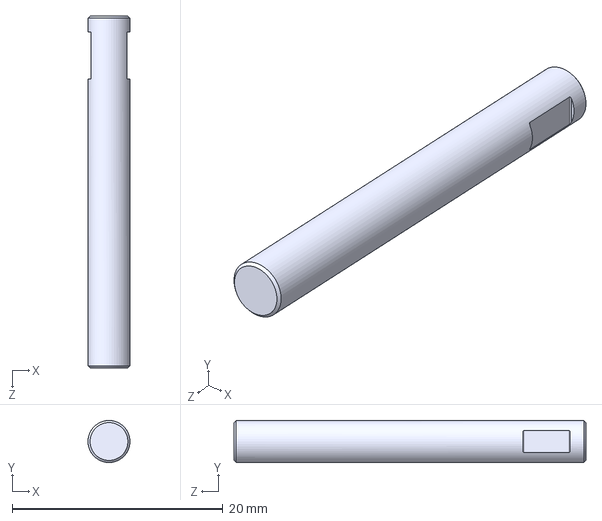
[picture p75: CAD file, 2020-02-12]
mechanics/actuator_module_v1/step_files/motor_antigravity_4004_custom_shaft.STEP
3.99 x 3.99 x 33.4 mm

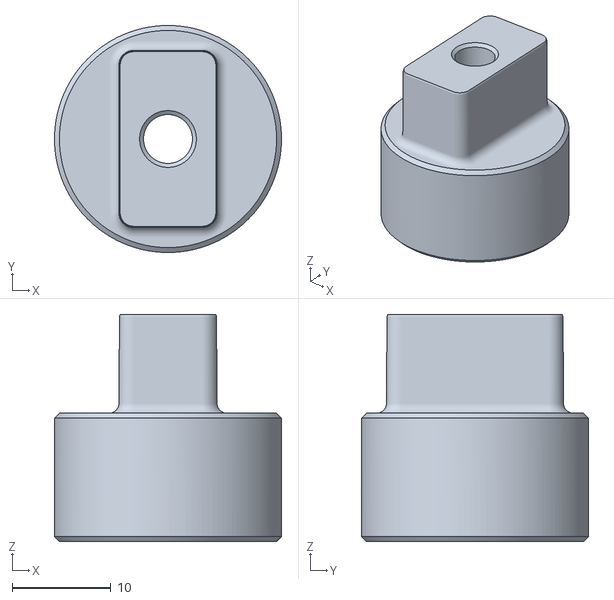
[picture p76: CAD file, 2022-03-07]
mechanics/actuator_module_v1/stl_files/tool_output_pulley_modification.STL
23.0 x 23.0 x 23.0

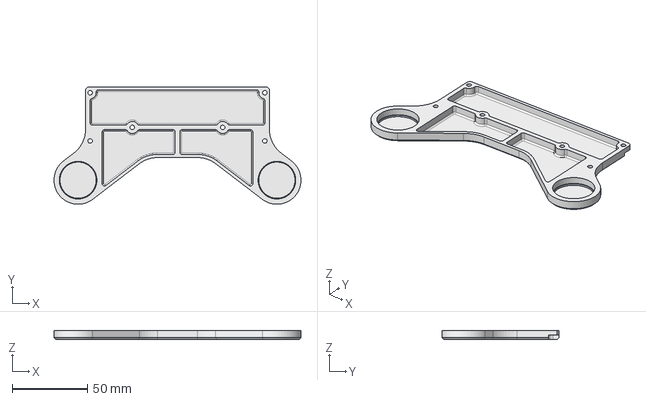
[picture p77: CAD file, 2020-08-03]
mechanics/biped_6dof_v1/cad_files/FreeCAD/body_structure_biped_front.FCStd
164.0 x 78.0 x 6.00 mm

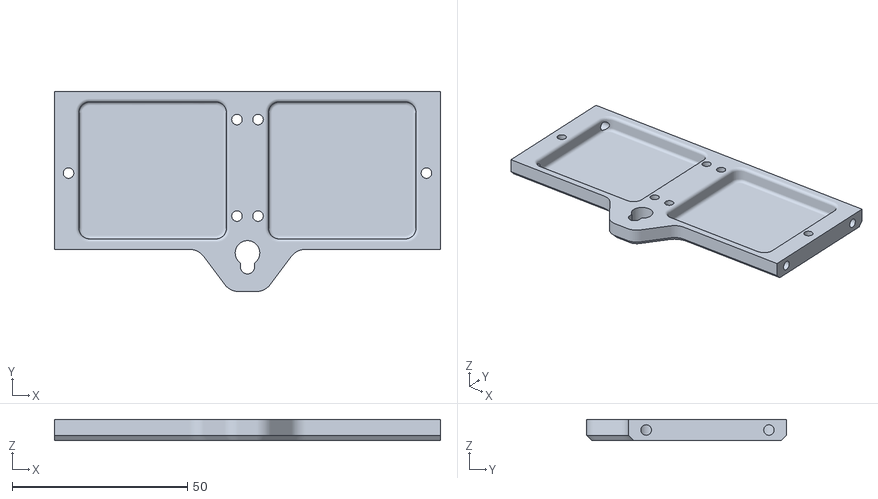
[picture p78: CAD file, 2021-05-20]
mechanics/biped_6dof_v1/stl_files/body_structure_biped_back_rev_a.STL
110.0 x 57.0 x 6.00

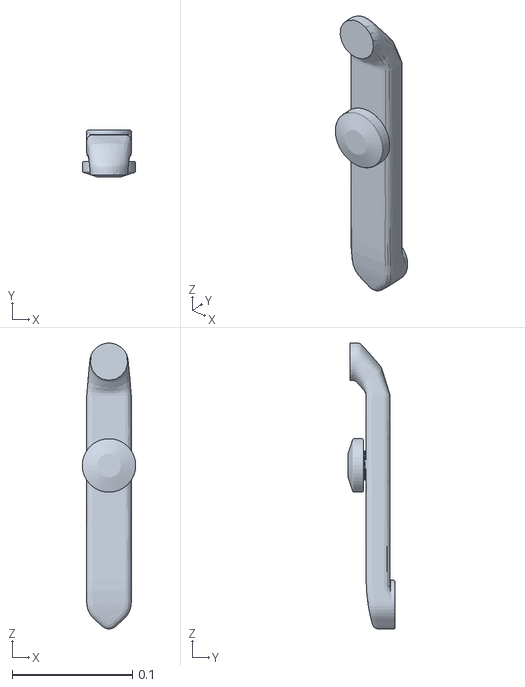
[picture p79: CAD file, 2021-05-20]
mechanics/biped_6dof_v1/stl_files_for_visualization/upper_leg_200mm_left_side.STL
0.0444 x 0.0389 x 0.237

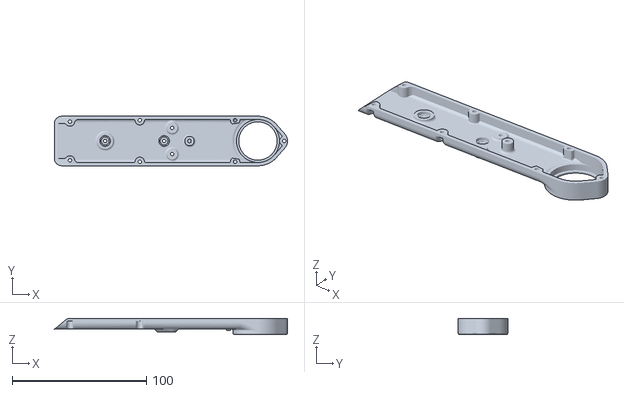
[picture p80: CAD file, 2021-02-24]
mechanics/biped_leg_3dof_v1/stl_files/upper_leg_structure_cover_200mm_rev_a.STL
173.5 x 37.0 x 12.0

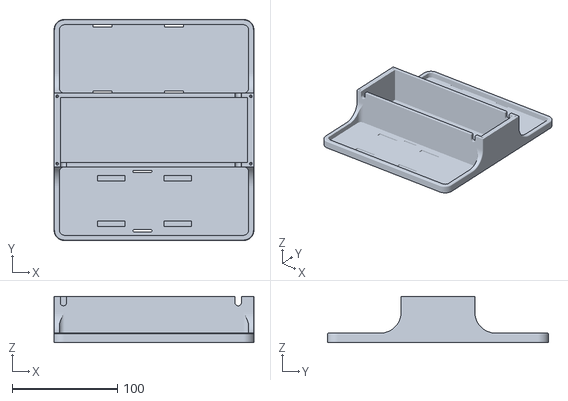
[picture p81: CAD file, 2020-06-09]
mechanics/dual_motor_testbed_v1/stl_files/electronics_box_base.STL
190.0 x 210.0 x 44.0

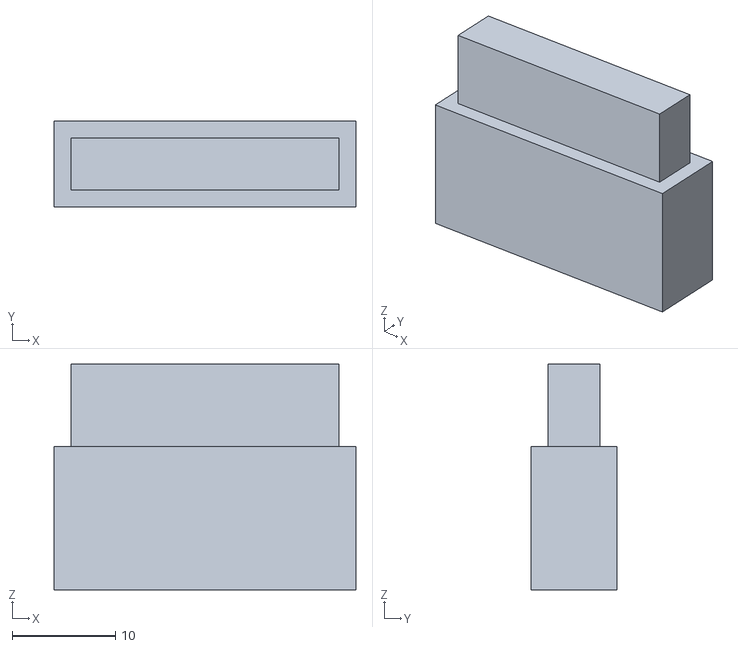
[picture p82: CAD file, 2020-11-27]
mechanics/finger_edu_v1/stl_files/ti_stack_support.STL
29.3 x 8.30 x 21.9

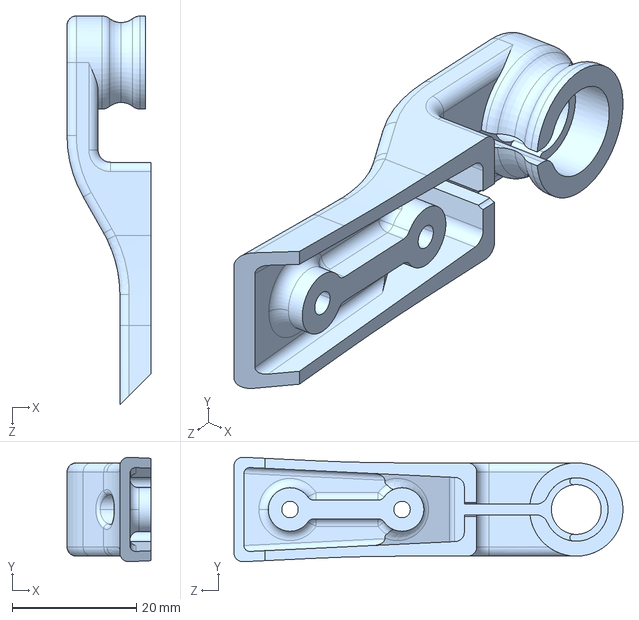
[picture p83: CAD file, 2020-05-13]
mechanics/foot_contact_switch_v1/step_files/lower_leg_structure_fork.STEP
13.5 x 16.8 x 62.5 mm

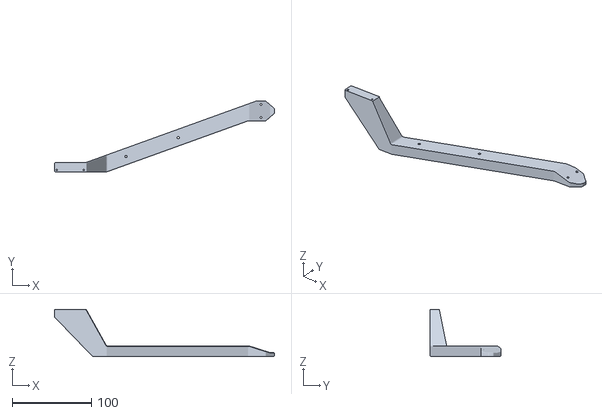
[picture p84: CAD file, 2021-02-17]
mechanics/general/stl_files/calibration_tool_biped_6dof_v1_mirror.STL
277.1 x 89.3 x 59.4

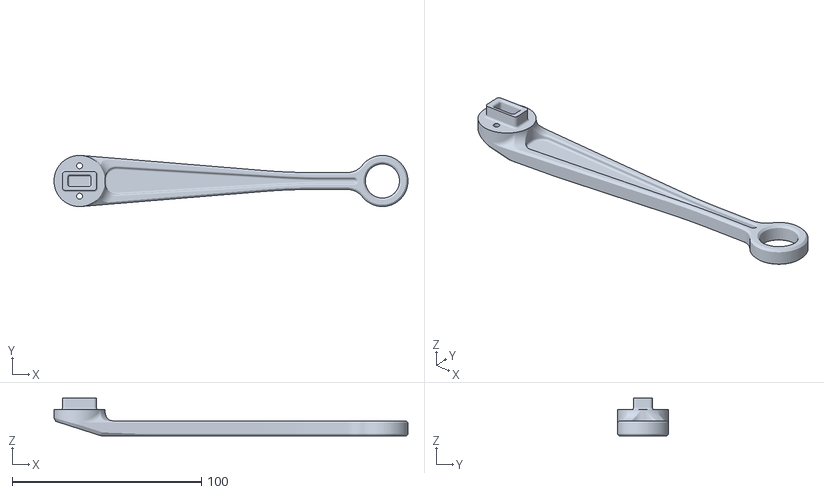
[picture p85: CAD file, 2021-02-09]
mechanics/leg_2dof_v2/stl_files/lower_leg_v3.STL
187.0 x 27.0 x 20.0

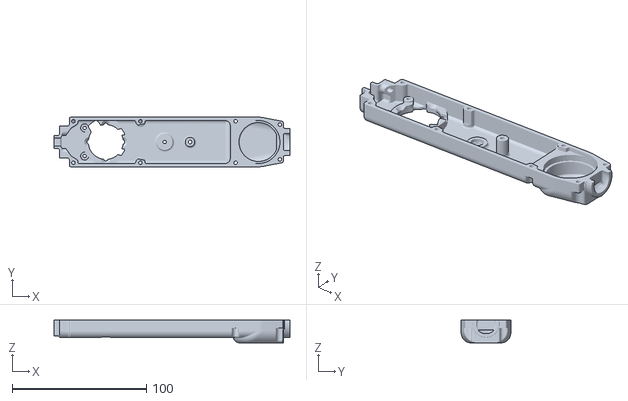
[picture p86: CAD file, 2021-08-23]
mechanics/leg_3dof_v1/stl_files/hip_fe_module_shell_base_alt_a.STL
175.9 x 37.0 x 17.0

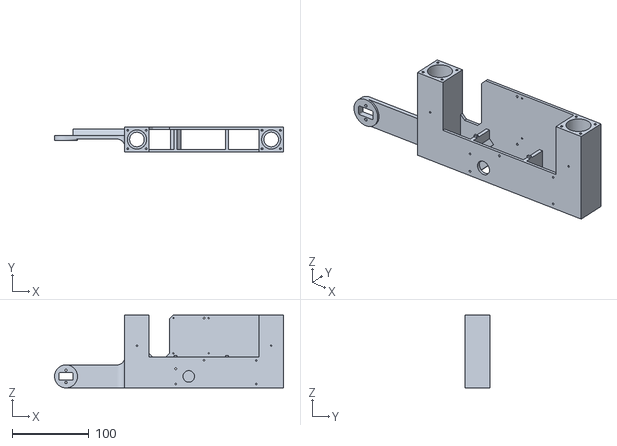
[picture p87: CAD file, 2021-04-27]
mechanics/leg_test_stand_v2/stl_files/carriage.STL
298.5 x 32.0 x 95.1

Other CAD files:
mechanics/nyu_finger_v1/stl_files/upper_leg_module_shell_cover.STL
mechanics/quadruped_robot_12dof_v1.1/stl_files/neo_pixel_cover.STL
mechanics/quadruped_robot_8dof_v2/stl_files/body_structure_top_roll_bar.STL
mechanics/quadruped_robot_8dof_v2/stl_files_for_visualization/solo8_v2_body.STL
mechanics/actuator_module_v1/step_files/transmission_pulley_at3_t10_center.STEP
mechanics/actuator_module_v1/step_files/transmission_pulley_at3_t10_motor.STEP
mechanics/actuator_module_v1/stl_files/encoder_codewheel_kit_mount.STL
mechanics/actuator_module_v1/stl_files/encoder_codewheel_pwb_mount.STL
mechanics/actuator_module_v1/stl_files/tool_center_pulley_protection.STL
mechanics/actuator_module_v1/stl_files/tool_code_wheel_bonding.STL
mechanics/actuator_module_v1/stl_files/tool_motor_shaft_extraction.STL
mechanics/actuator_module_v1/stl_files/tool_motor_shaft_pulley_bonding.STL
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

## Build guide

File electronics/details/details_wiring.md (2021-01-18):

# Details Wiring
## Actuator Module Wiring
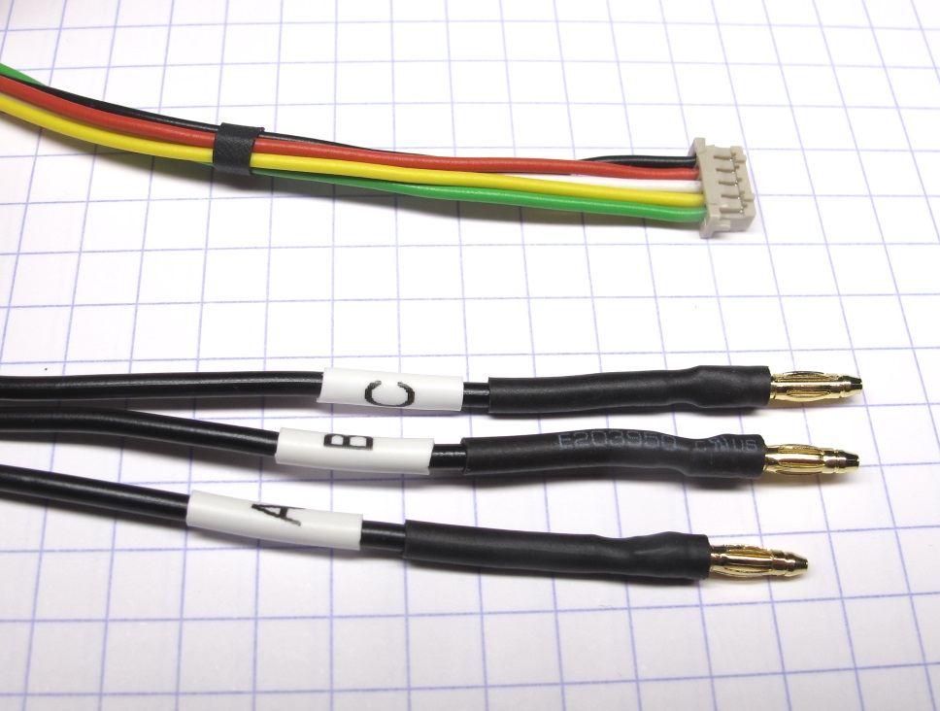
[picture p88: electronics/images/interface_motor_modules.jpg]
 <br>*Electrical connection actuator modules*<br>

* the electrical interface of the actuator modules consists of a 5 pole encoder wire and 3 motor phase wires
* for the encoder wires we use [0,14 mm² Kabeltronik wires](details_components.md#kabeltronik-encoder-wires) with a [5 pole Hirose DF13 connector](details_components.md#hirose-df13-sockets)
* for crimping the wires you will need the [DF13 crimp terminals](details_components.md#hirose-df13-crimp-terminals) and the [Hirose DF13 crimp tool](details_components.md#hirose-crimp-tool)
* the color code and pin assignment is documented below
* for the motor phase wires we use [0,50 mm² Kabeltronik wires](details_components.md#motor-phase-wires) with [2mm Reely gold connectors](details_components.md#motor-phase-connectors)
* we measure the wire length of the actuator modules from the surface where the wires exit the shell to the connector interface

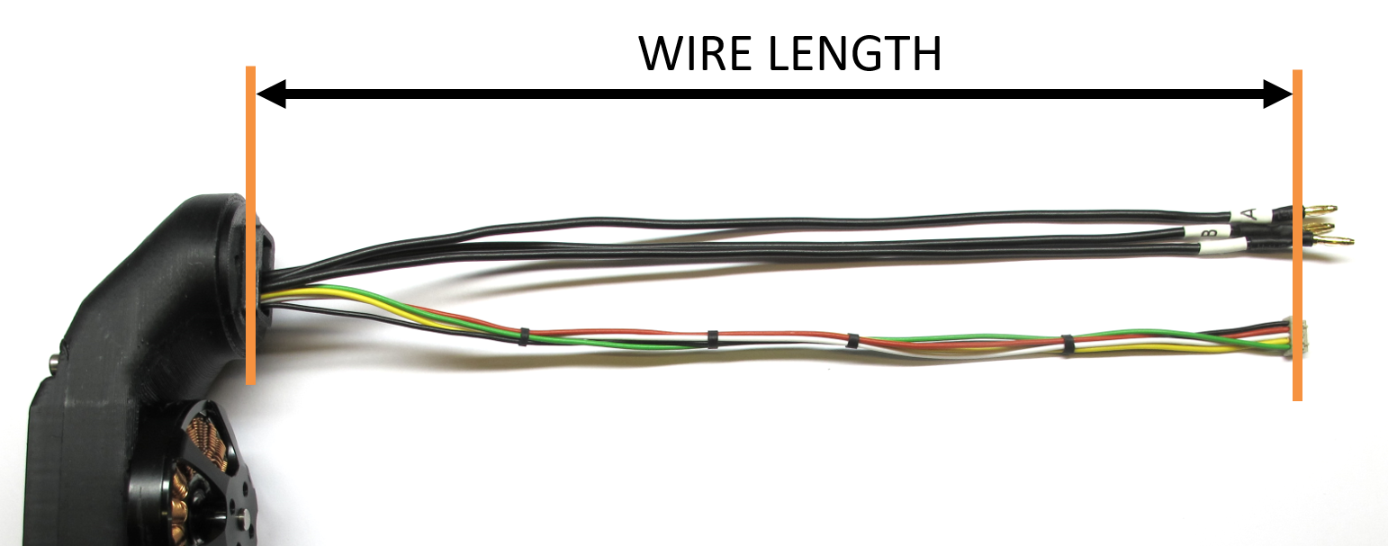
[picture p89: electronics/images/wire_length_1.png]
 <br>*Wire length actuator modules*<br>

 <br>*Encoder wiring with Kabeltronik wires*

## Micro Driver Board Wiring
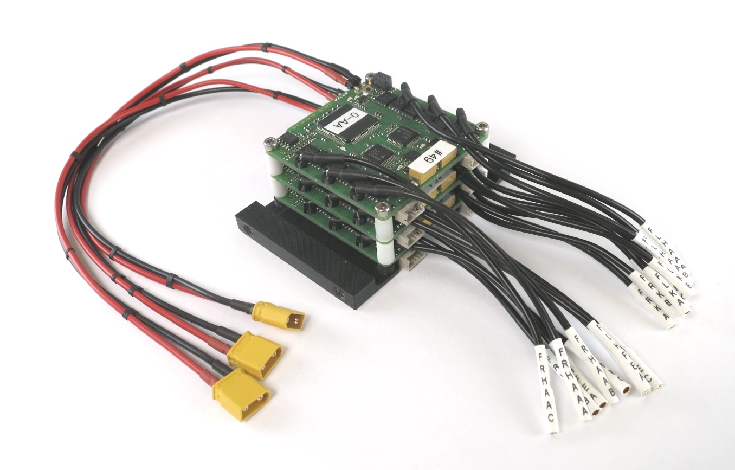
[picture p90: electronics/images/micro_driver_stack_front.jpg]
 <br>*Fully assembled micro driver stack*<br>

* we use [right angle pin headers](details_components.md#right-angle-pin-headers) for connecting the motor phase and power wires to the micro driver board
* for the motor phase wires we use [0,50 mm² Kabeltronik wires](details_components.md#motor-phase-wires) with [2mm Reely gold connectors](details_components.md#motor-phase-connectors)
* for the power supply wires wie use [0,50 mm² Kabeltronik wires](details_components.md#motor-phase-wires) with [XT30 power connectors](details_components.md#power-connectors)
* we measure the wire length of the electronics from the edge of the electronis board to the connector interface.

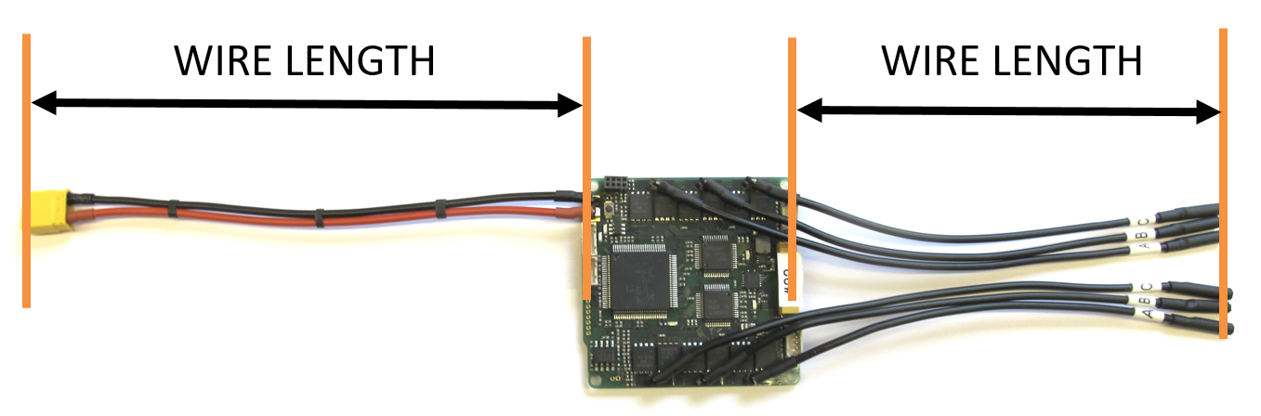
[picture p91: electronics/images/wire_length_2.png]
 <br>*Wire length electronics boards*<br>

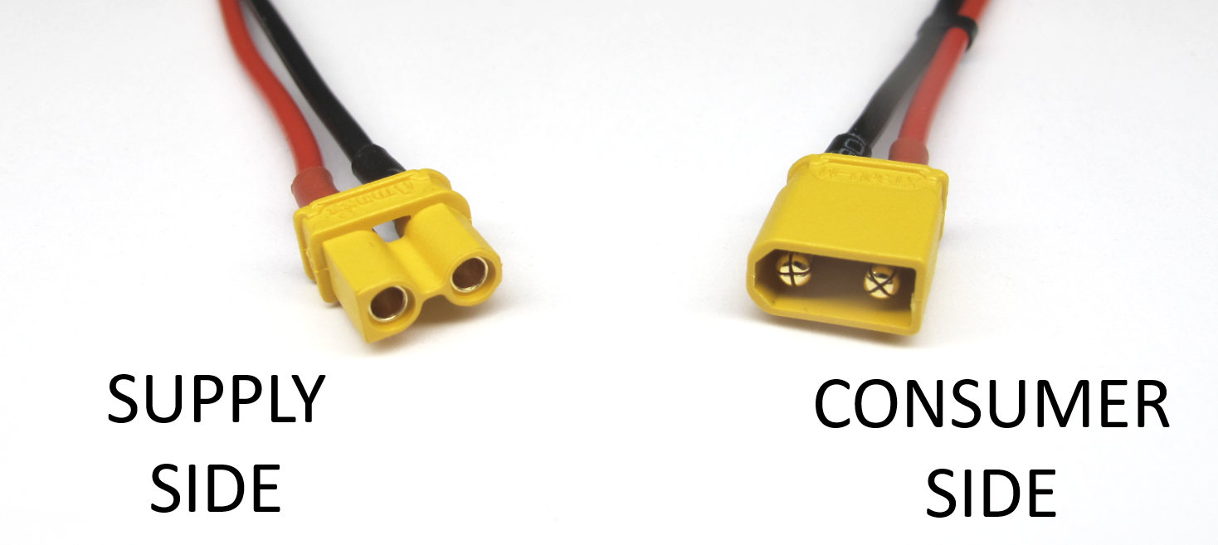
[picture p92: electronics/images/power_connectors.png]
<br>*Convention power connectors*<br>

---
## SPI Wires
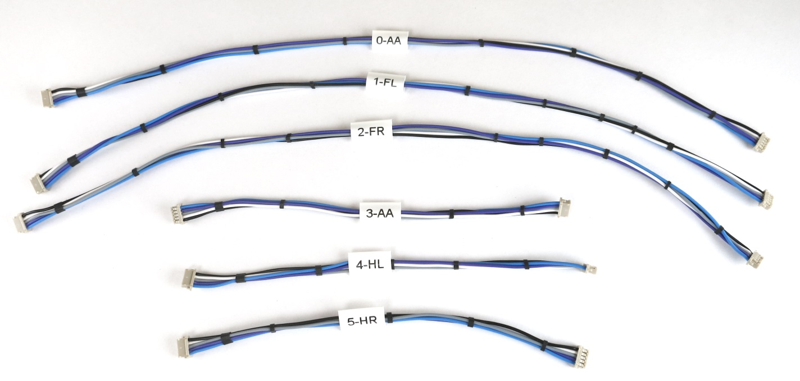
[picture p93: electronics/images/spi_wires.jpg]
 <br>

* for the SPI connections between the master board and the micro driver boards we use [0,14 mm² Kabeltronik wires](details_components.md#kabeltronik-encoder-wires) with two [5 pole Hirose DF13 connectors](details_components.md#hirose-df13-sockets)
* for crimping the wires you will need the [DF13 crimp terminals](details_components.md#hirose-df13-crimp-terminals) and the [Hirose DF13 crimp tool](details_components.md#hirose-crimp-tool)
* the color code and pin assignment is documented below
* the spi bus operates at high frequencies - keep the wires short

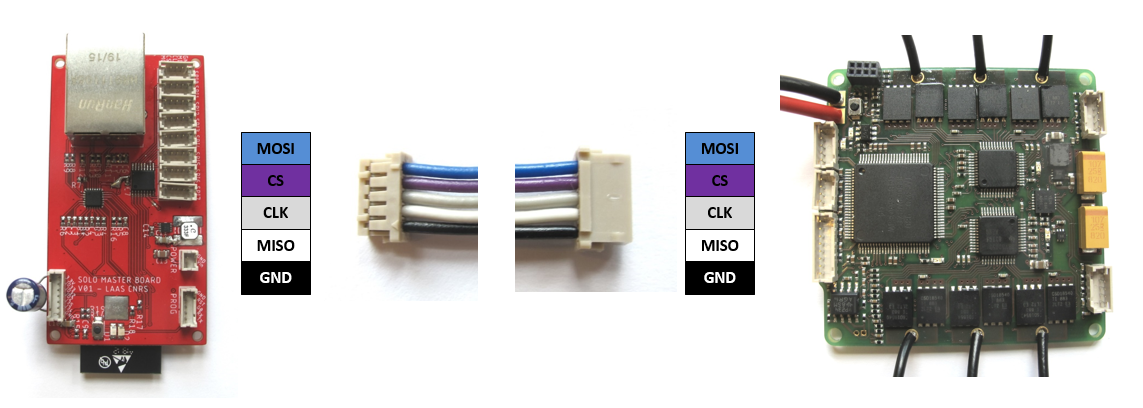
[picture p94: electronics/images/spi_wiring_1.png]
 <br>*SPI bus connection between the master board and the micro driver boards*

---
## IMU Wire
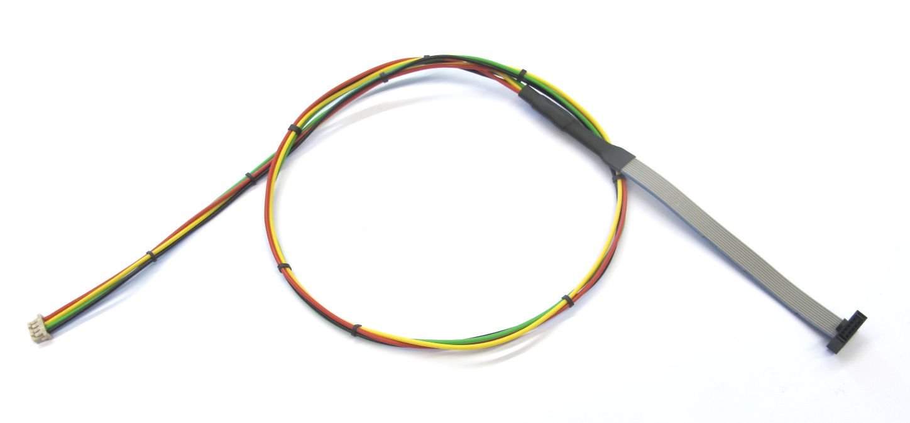
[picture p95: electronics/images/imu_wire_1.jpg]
<br>*Wire for Inertia Measurement Unit*<br>

* for connecting the inertia measurement unit to the master board we use a [ribbon cable with a 10 pin rectangular connector](details_components.md#imu-cable) and extension wires with a [4 pin Hirose connector](details_components.md#hirose-df13-sockets)
* the pin assignment is documented here: [Master Board Wiring](https://github.com/open-dynamic-robot-initiative/master-board/blob/master/documentation/masterboard_wiring.md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)
---
## Robot Interface Wire
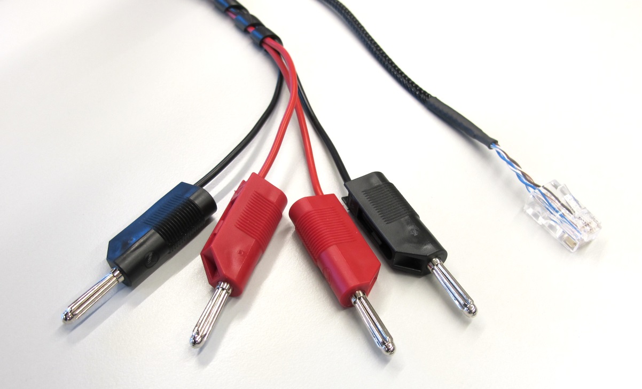
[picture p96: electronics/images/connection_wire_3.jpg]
<br>*Robot Interface Wire - Supply Side*<br>

* for powering the robots we use [1 mm² Kabeltronik wires](details_components.md#power-connectors-and-cable) with [4mm power connectors](details_components.md#power-connectors-and-cable) on the supply side
* to reduce the diameter and stiffness of the wire we use a self-made 4 pole ethernet wire
* the color code and pin assignment is documented below - the ethernet connectors are identical on both sides
* for crimping the [ethernet connectors](details_components.md#ethernet-connector) you will need the corresponding [crimp tool](details_components.md#crimp-tool-ethernet-connector)
* you can use a standard ethernet wire instead

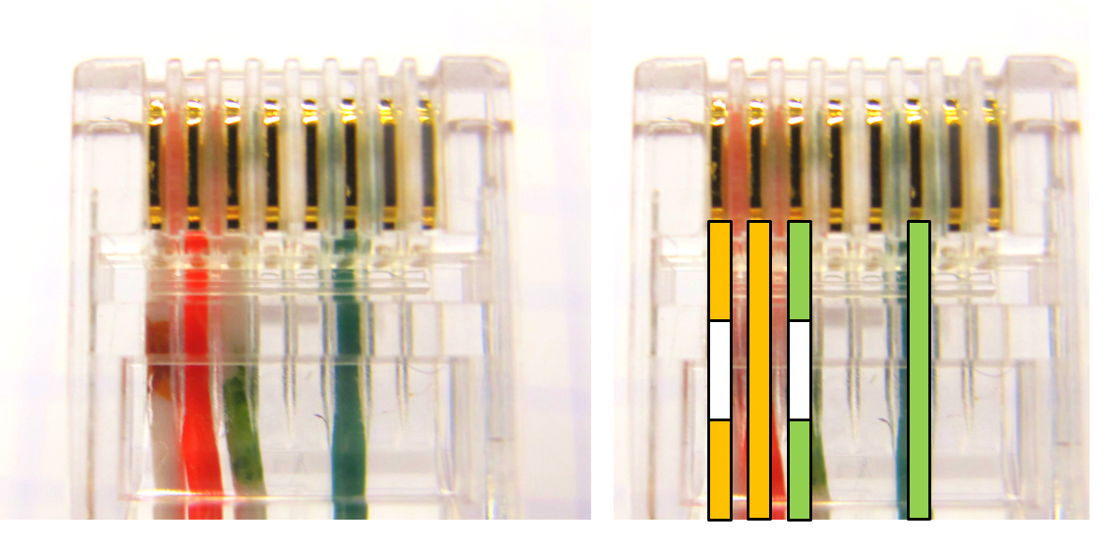
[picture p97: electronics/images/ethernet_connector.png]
<br>*Self-made ethernet wire with 4 connections*<br>

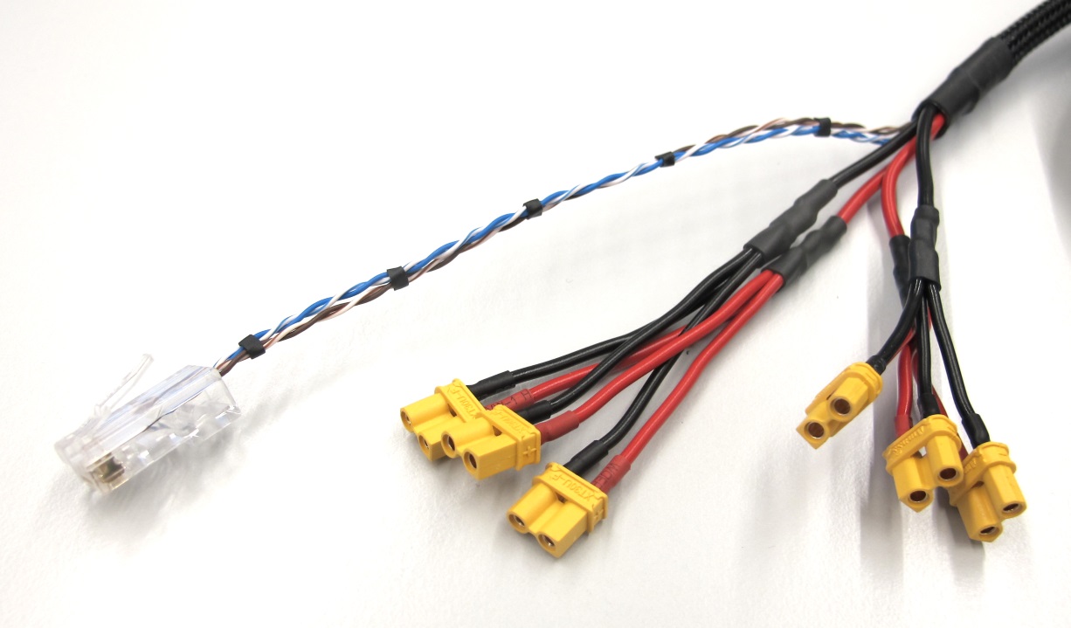
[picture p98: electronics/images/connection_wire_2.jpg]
<br>*Robot Interface Wire - Robot Side*<br>

* for powering the robots we use [1 mm² Kabeltronik wires](details_components.md#power-connectors-and-cable) with [XT30 power connectors](details_components.md#power-connectors) on the robot side

<br>*Convention power connectors*<br>

---
## Wiring Ribbon Cables- Encoder to Micro Driver Electronics
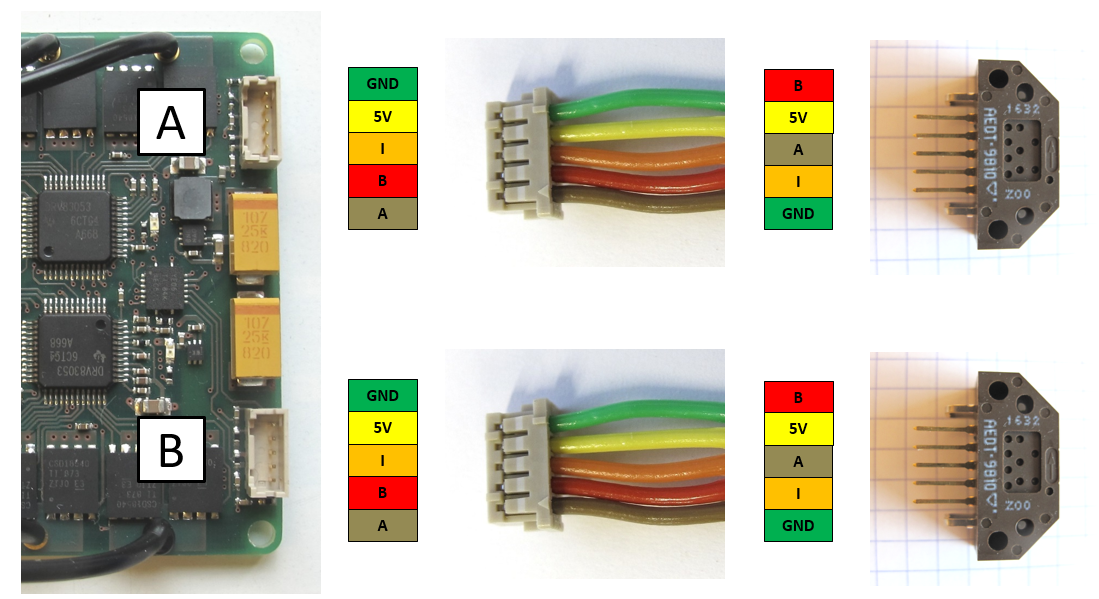
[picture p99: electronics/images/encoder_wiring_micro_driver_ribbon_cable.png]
 <br>*Encoder wiring with ribbon cables*

---
## Wiring Ribbon Cables - Encoder to TI Launchpad
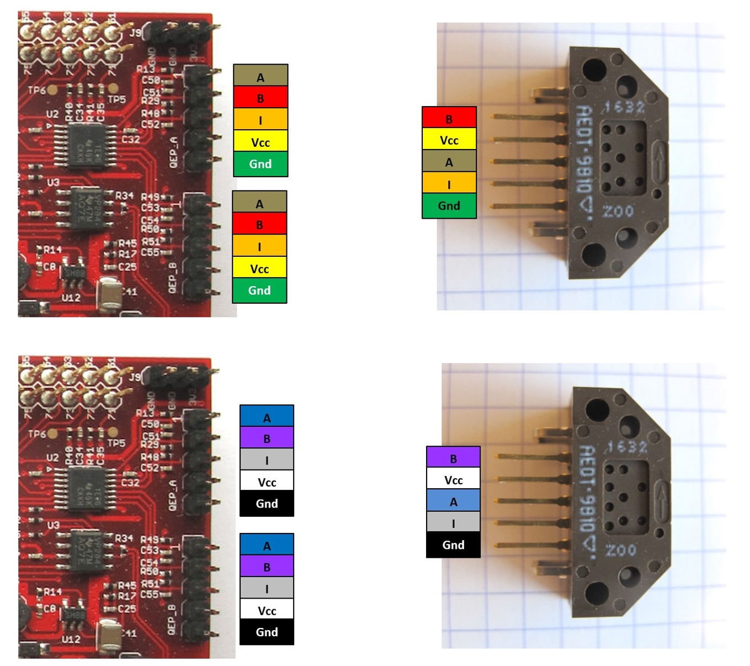
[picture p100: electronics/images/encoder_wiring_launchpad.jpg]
 <br>*Encoder wiring with ribbon cables*

---
## Wiring - Foot Sensor
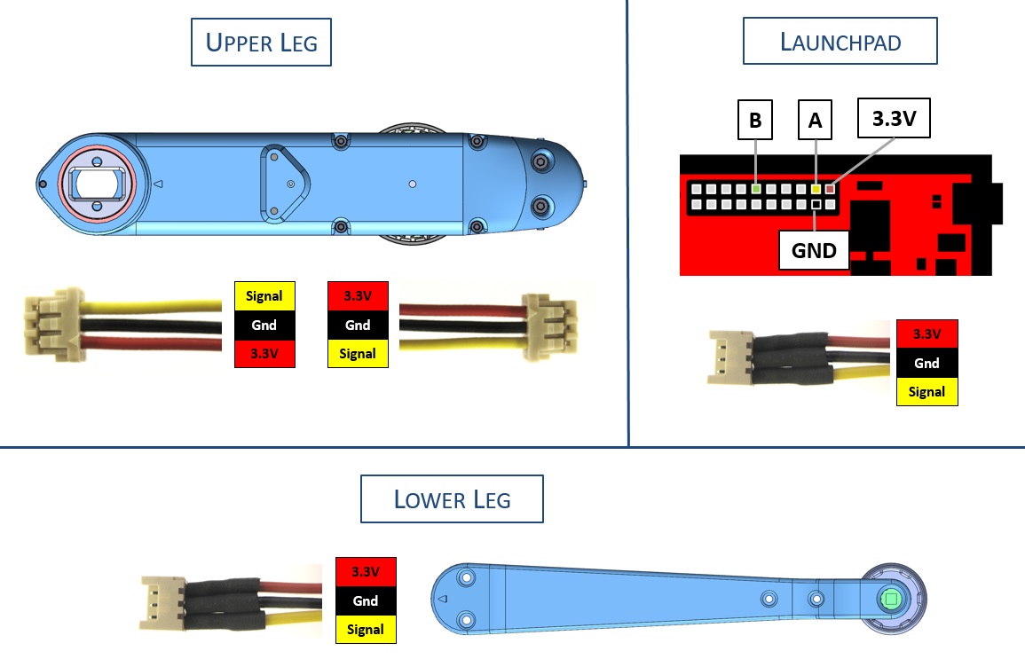
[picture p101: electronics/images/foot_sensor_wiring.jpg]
 <br>*Foot sensor wiring*

---
## CAN Connector Wiring
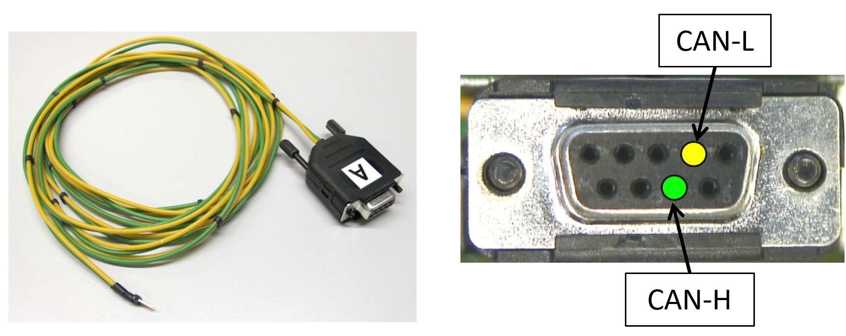
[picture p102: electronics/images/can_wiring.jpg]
 <br>*CAN connector wiring*

* for communicating with the Texas Instruments Evaluation Boards we use a 2 pole wire with a [9 pin D-sub connector](details_components.md#can-connector)
* on the computer side we use a [PEAK PCI Express CAN card](details_components.md#can-card)

---
## More Information
[Open Dynamic Robot Initiative - Webpage](https://open-dynamic-robot-initiative.github.io)  
[Open Dynamic Robot Initiative - YouTube Channel](https://www.youtube.com/channel/UCx32JW2oIrax47Gjq8zNI-w)   
[Open Dynamic Robot Initiative - Forum](https://odri.discourse.group/categories)  
[Open Dynamic Robot Initiative - Paper](https://arxiv.org/pdf/1910.00093.pdf)  
[Hardware Overview](../../README.md#open-robot-actuator-hardware)  
[Software Overview](https://github.com/open-dynamic-robot-initiative/open-dynamic-robot-initiative.github.io/wiki)  
[Back to Electronics](../README.md)  

## Authors
Felix Grimminger

## License
BSD 3-Clause License

## Copyright
Copyright (c) 2019-2020, Max Planck Gesellschaft and New York University

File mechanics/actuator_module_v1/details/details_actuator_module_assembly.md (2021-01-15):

# Details Actuator Module Assembly
## Description
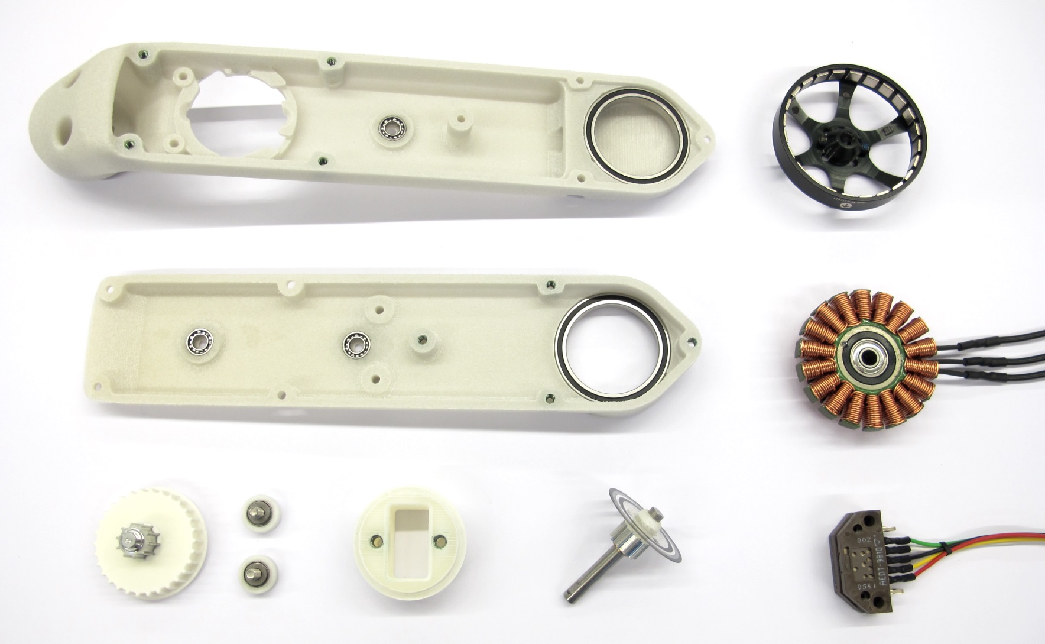
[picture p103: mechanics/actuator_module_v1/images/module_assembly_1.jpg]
 <br>*Starting Point: The six sub-assemblies that were prepared in the previous steps.*

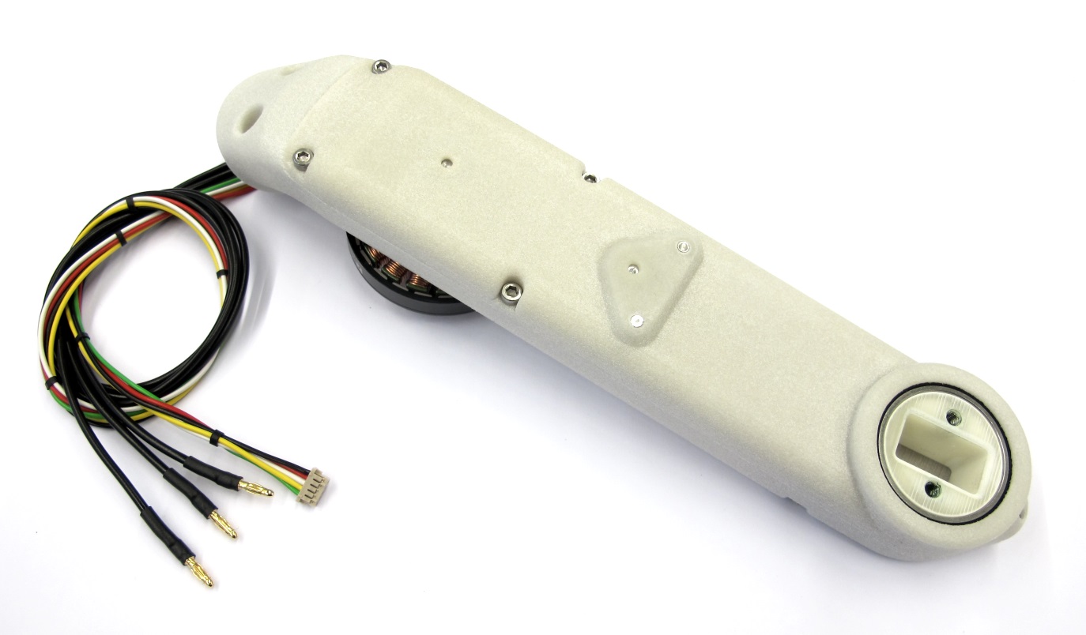
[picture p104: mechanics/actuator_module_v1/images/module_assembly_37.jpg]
 <br>*End Result: Fully assembled actuator module.<br>Weight with 30cm wires: 160g*

* this page describes how to assemble the actuator modules
* the 6 sub-assemblies that were prepared before are required for this step
* instructions on how to prepare the subassemblies can be found here: [step-by-step-instructions](#step-by-step-instructions)
* in addition to the subassemblies the following components are required

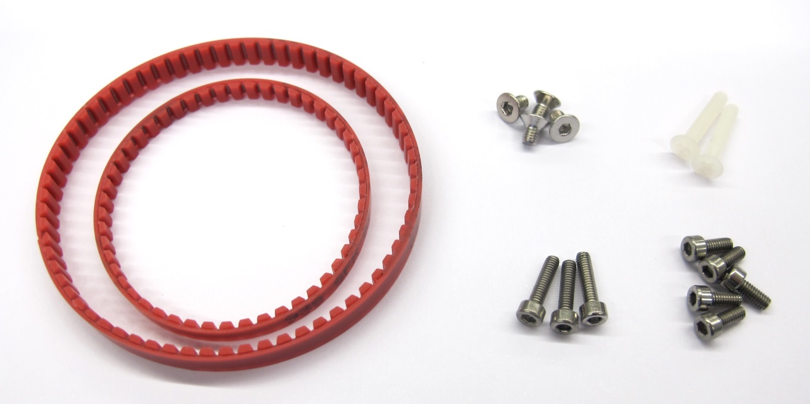
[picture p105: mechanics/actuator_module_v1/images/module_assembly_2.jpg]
 <br>*Aditionally required components*<br>
* 1 x Timing Belt AT3 150mm - width 4mm
* 1 x Timing Belt AT3 201mm - width 6mm
* 4 x M3x5 Flat Head Screw for motor attachment
* 2 x M3x16 Flat Head Screw for encoder attachment
* 5 x M2,5x6 Socket Head Cap Screw and <br>
3 x M2,5x8 Socket Head Cap Screw for connecting the shells

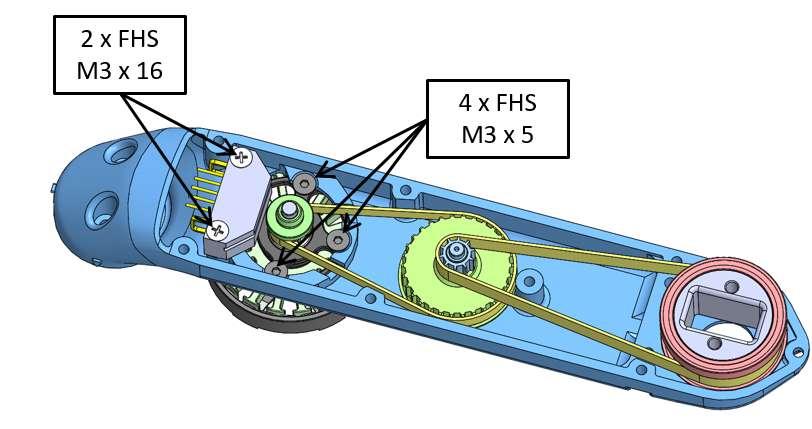
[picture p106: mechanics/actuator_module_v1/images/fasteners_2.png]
 <br>*Fasteners for Actuator Module Assembly<br>FHS = Flat Head Screw*

---
### Mounting the Stator
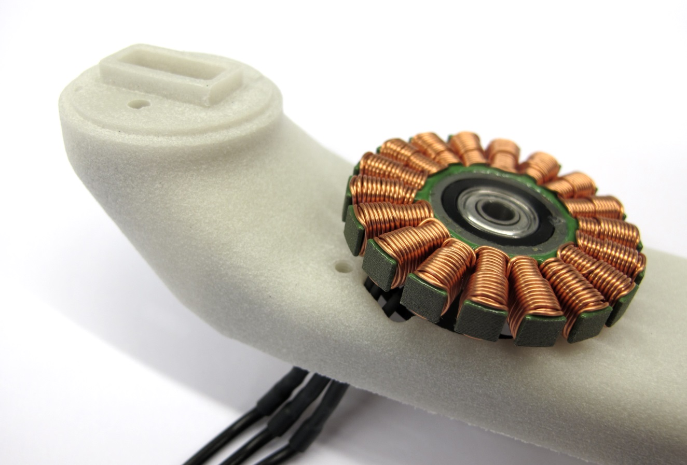
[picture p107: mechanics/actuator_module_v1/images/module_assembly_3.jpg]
 <br>*Route the motor phase wires through the opening in the shell.<br>Place the stator on the mounting surface.*

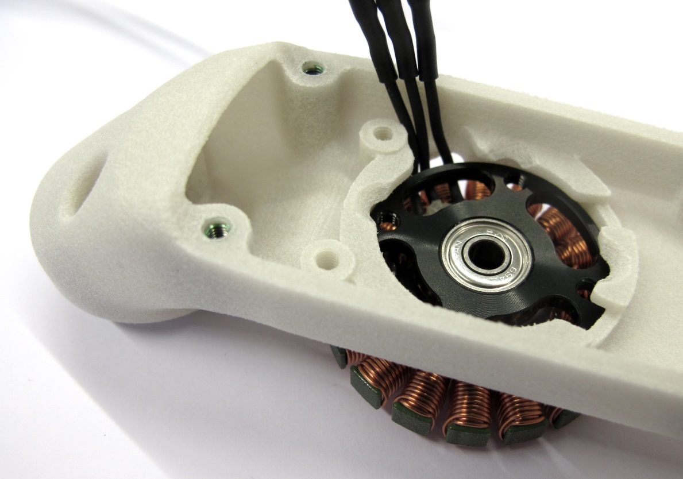
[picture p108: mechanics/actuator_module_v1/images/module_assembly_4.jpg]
 <br>*Bend the motor phase wires up and align them with the cutout as shown in the picture.*

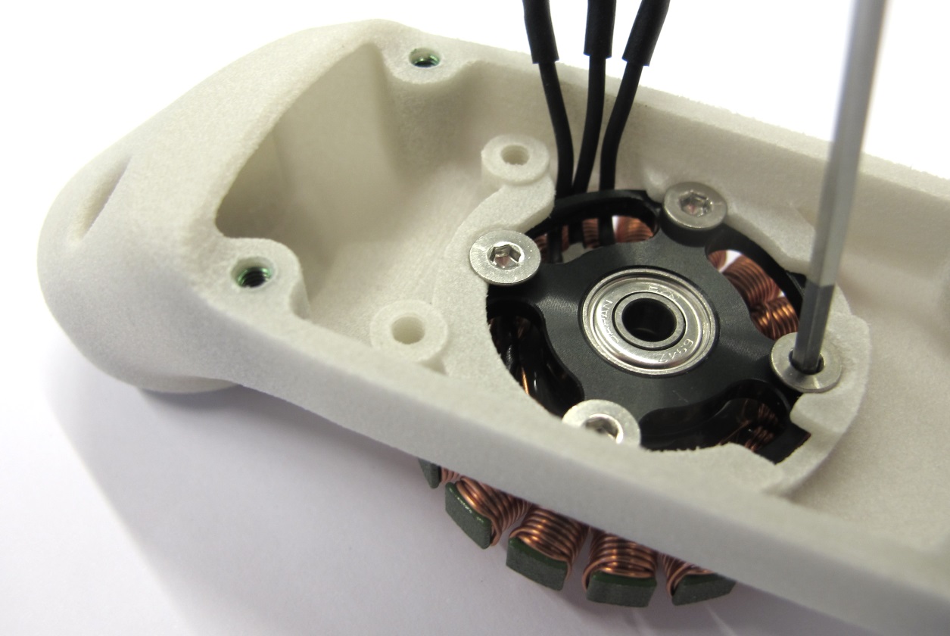
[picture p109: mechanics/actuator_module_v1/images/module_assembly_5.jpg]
 <br>*Use a 2mm hex driver to install the four M3x5 flat head screws.<br> Make sure that the stator is fully seated and doesn't move.*

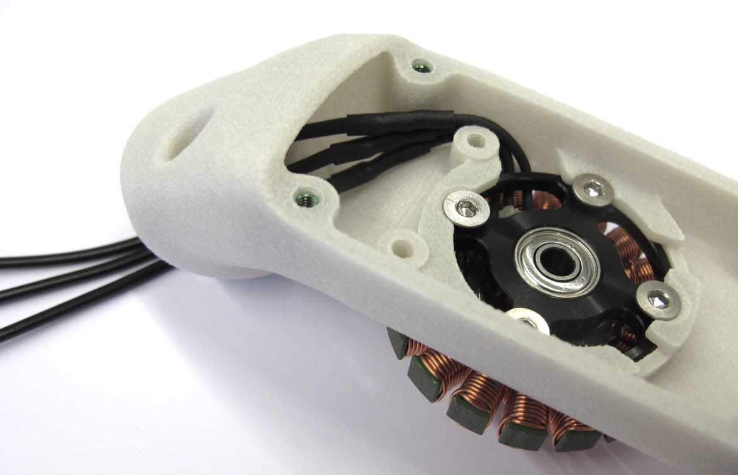
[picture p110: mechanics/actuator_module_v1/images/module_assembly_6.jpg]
 <br>*Route the phase wires through the opening behind the encoder mount and exit through the mounting interface.*

### Installing the Motor Shaft and Rotor

 <br>*For the next step you will need the motor shaft assembly.<br>Handle the codewheel with care and avoid bending or scratching it during the following steps.*

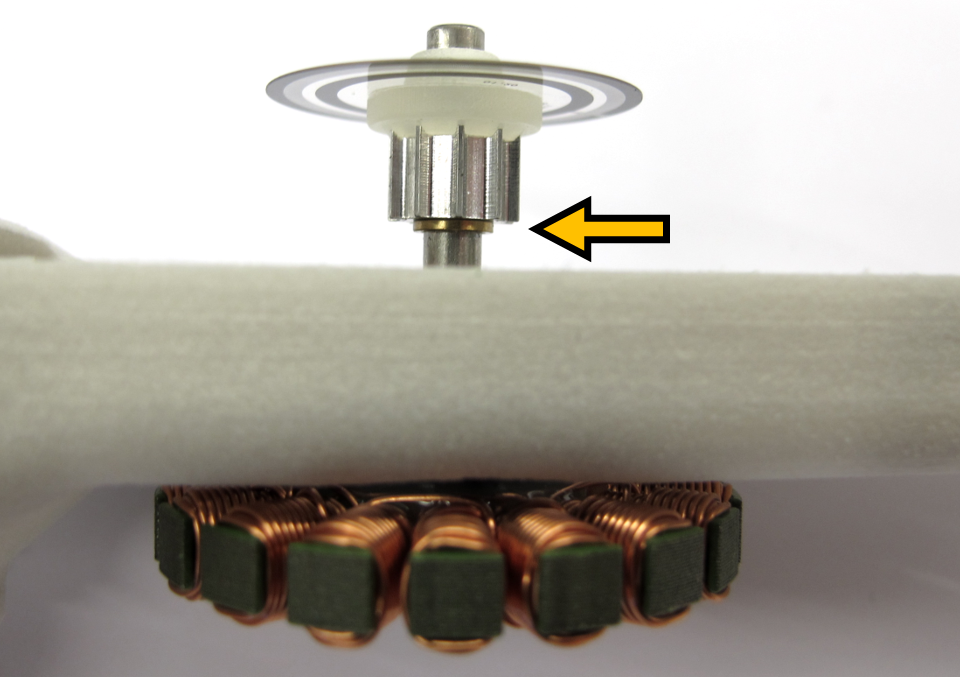
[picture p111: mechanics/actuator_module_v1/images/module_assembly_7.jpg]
 <br>*Insert the motor shaft assembly into the stator bearing.<br>Make sure that the brass spacer is installed.*

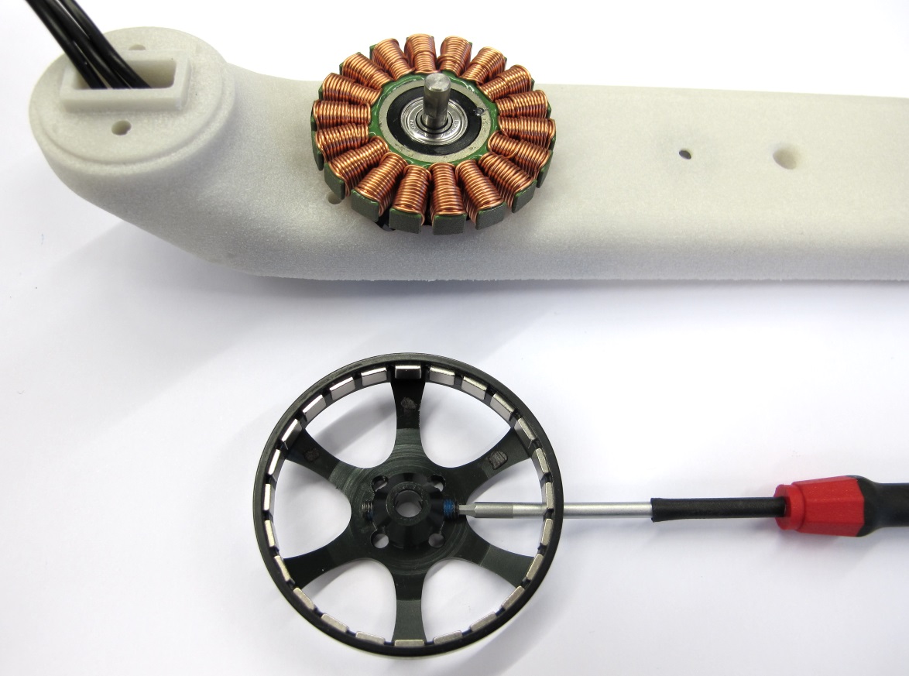
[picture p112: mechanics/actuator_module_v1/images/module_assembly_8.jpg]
 <br>*Turn the assembly around.<br> Use a 1,5mm hex driver to install the two M3 setscrews half way.*

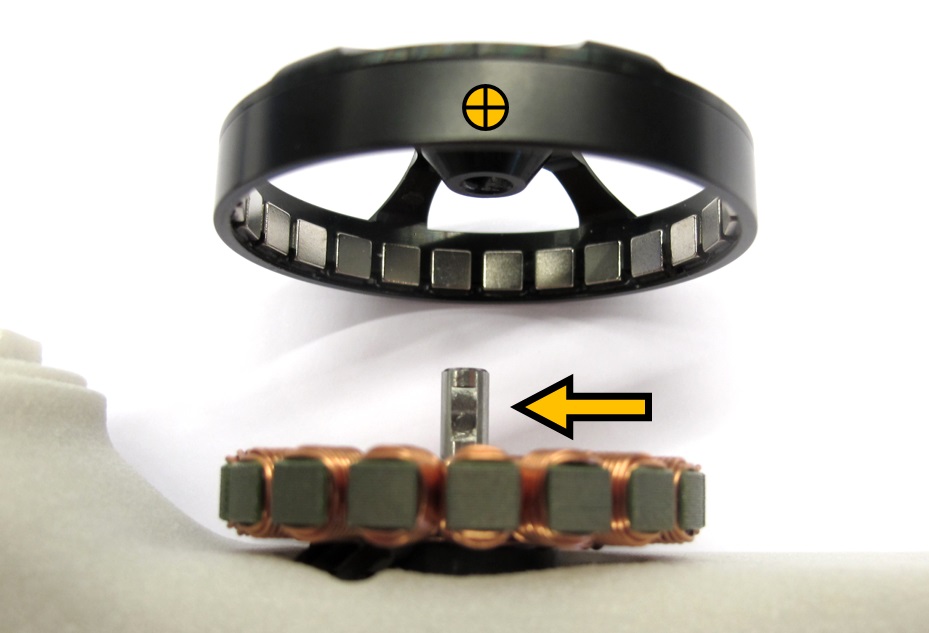
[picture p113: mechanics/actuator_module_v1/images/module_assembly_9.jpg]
 <br>*Line up the setscrews on the rotor with the flats on the motor shaft.<br> Install the rotor and push it all the way down.*

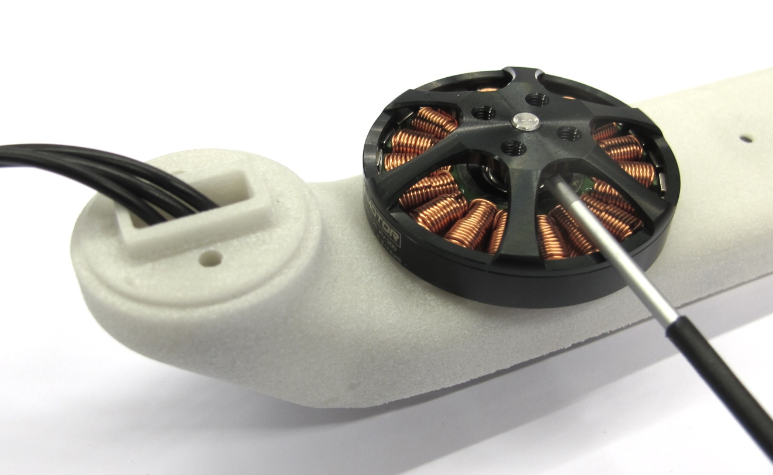
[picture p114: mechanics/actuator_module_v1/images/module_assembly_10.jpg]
 <br>*Tighten both setscrews using a 1,5mm hex driver while pushing down on the rotor.<br>Manually spinn the rotor to make sure that it runs freely.<br>Pull on the rotor in the axial direction - there should be no or only minimal play.*

### Installing the Timing Belt Transmission
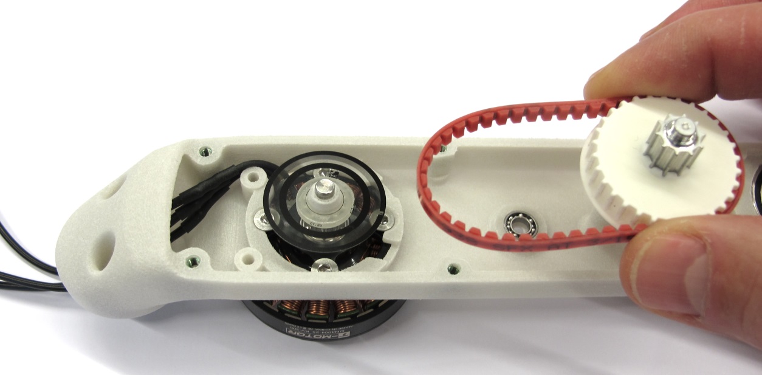
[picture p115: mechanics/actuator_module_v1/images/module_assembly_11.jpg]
 <br>*Place the 150mm timing belt on the center pulley and engage the teeth.*

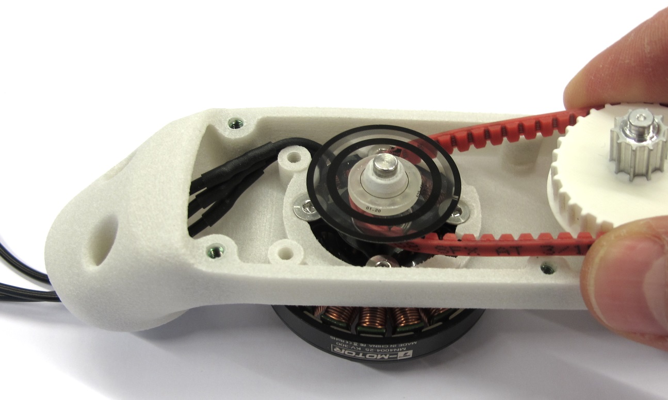
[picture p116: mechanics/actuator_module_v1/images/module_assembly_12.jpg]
 <br>*Place the timing belt on the motor pulley and engage the teeth.*

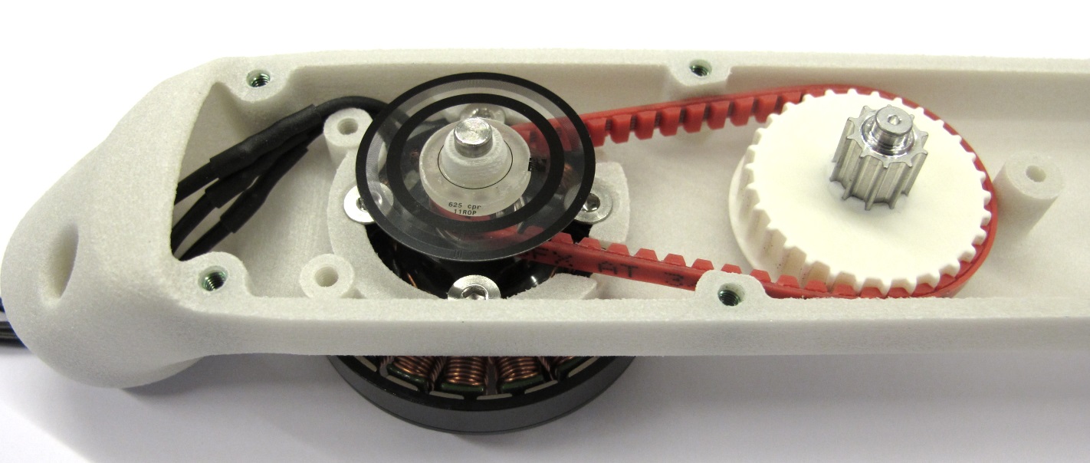
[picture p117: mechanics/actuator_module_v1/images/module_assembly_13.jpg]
 <br>*Keep the timing belt under tension and insert the center pulley into the bearing.*

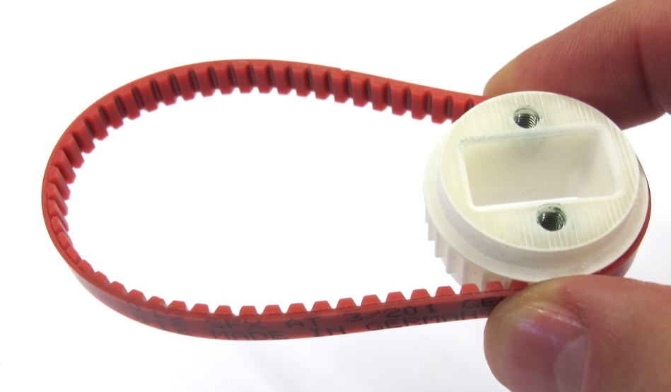
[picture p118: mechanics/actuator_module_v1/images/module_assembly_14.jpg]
 <br>*Place the 201mm timing belt on the output pulley and engage the teeth.<br>Make sure that the side with the flange is facing upwards.*

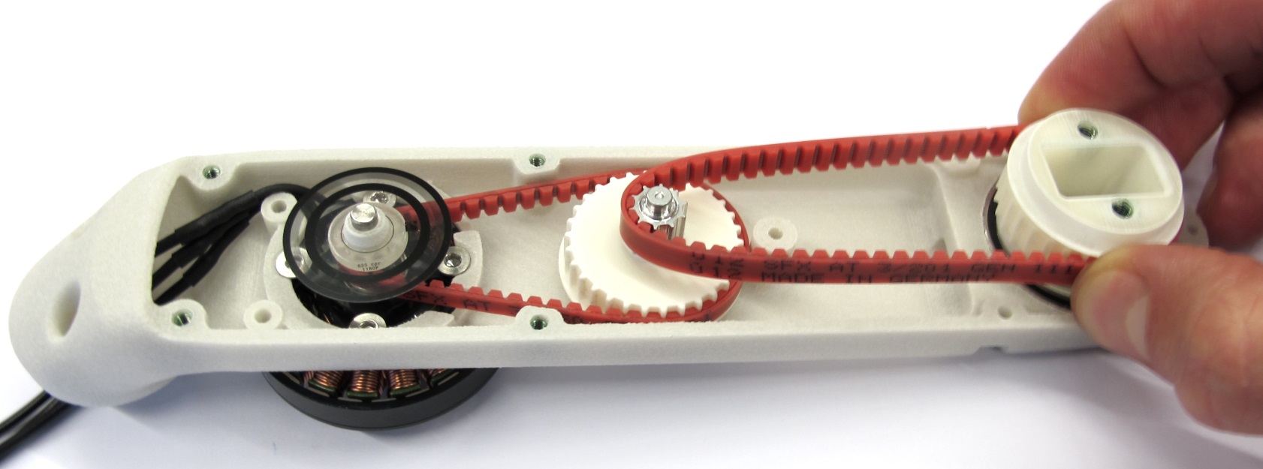
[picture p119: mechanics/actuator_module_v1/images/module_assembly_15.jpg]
 <br>*Place the timing belt on the center pulley and engage the teeth.<br>Keep the timing belt under tension and insert the output pulley into the bearing.*

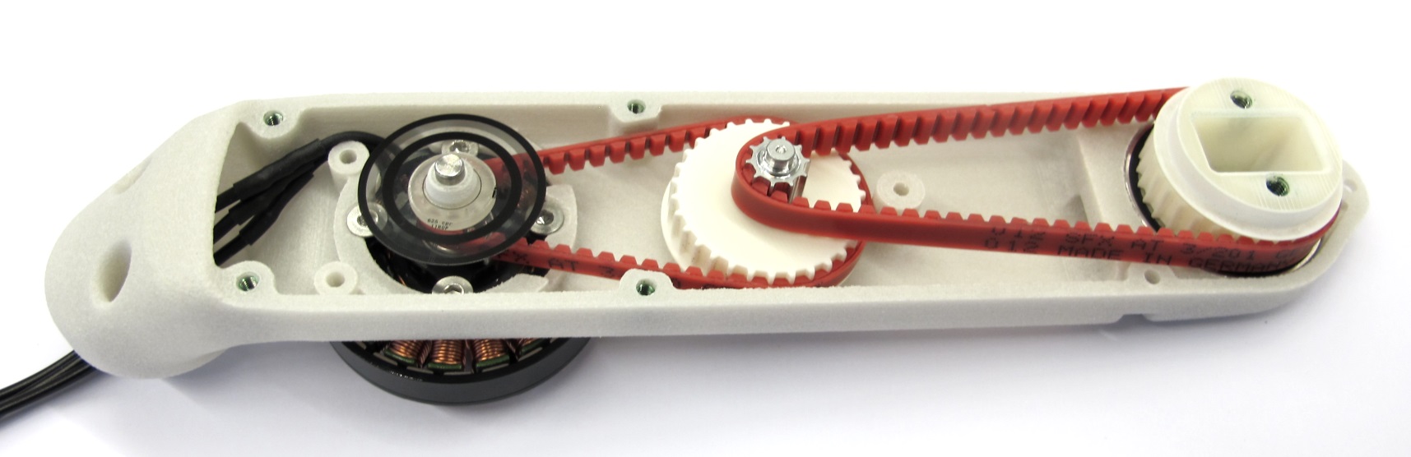
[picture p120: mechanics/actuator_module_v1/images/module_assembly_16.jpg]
 <br>*The timing belt transmission is now completed.<br>Rotate the output shaft back and forth and check if the transmission moves as expected.*

### Installing the Encoder

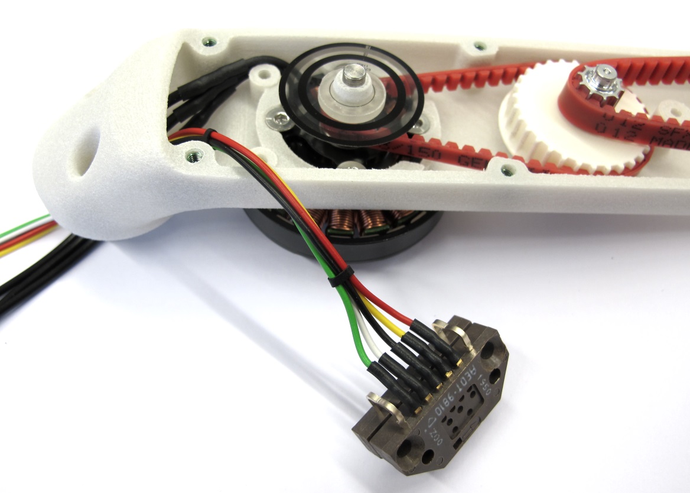
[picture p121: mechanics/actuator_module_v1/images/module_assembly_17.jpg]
 <br>*For this step you will need the encoder.<br>Route the encoder wires through the opening in the interface.*

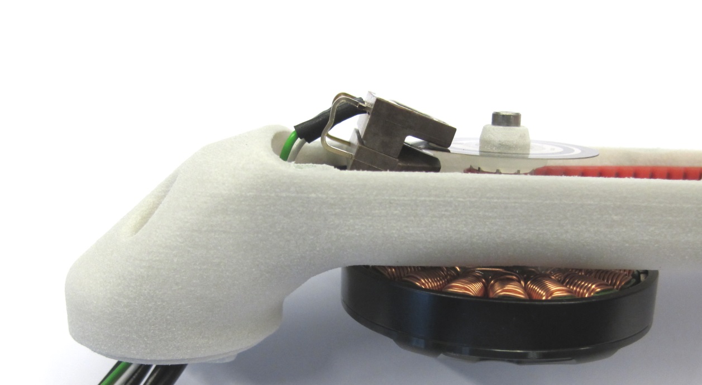
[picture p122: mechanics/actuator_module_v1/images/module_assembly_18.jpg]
 <br>*Carefully insert the encoder under an angle such that the codewheel is located in the gap.<br>We shorten and bend the encoder pins to simplify the assembly.*

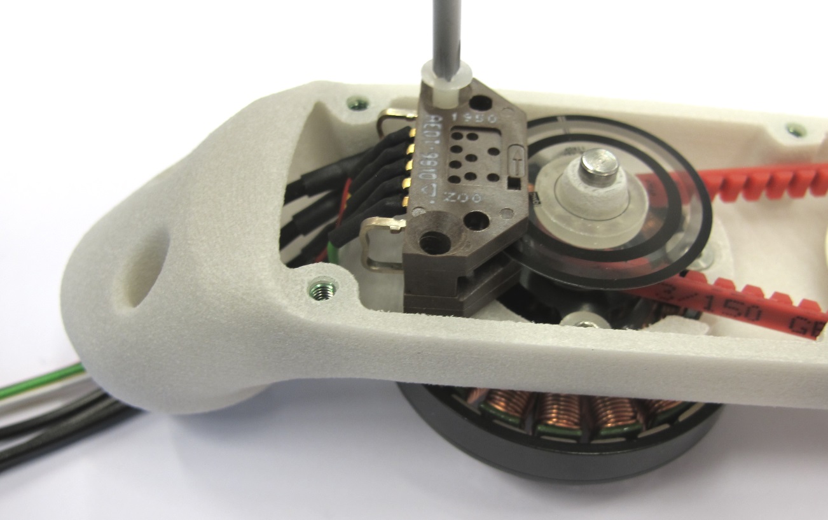
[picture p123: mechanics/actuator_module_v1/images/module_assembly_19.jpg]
 <br>*Place the encoder on the mounting surface and install the two M3x16 screws.*

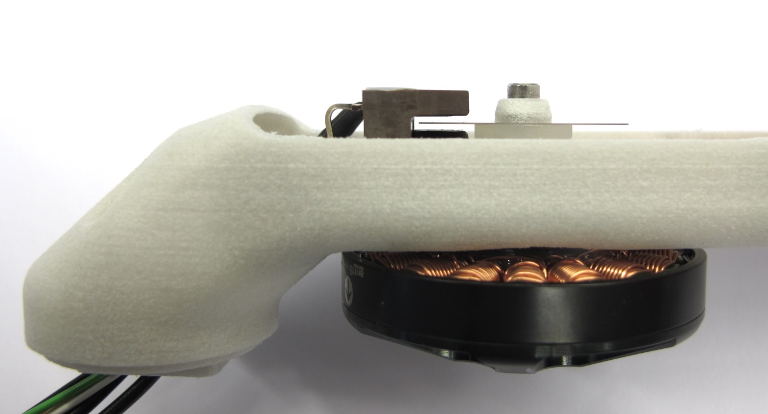
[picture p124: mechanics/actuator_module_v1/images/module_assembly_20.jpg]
 <br>*Make sure that the codewheel is located correctly and doesn't touch the encoder.*

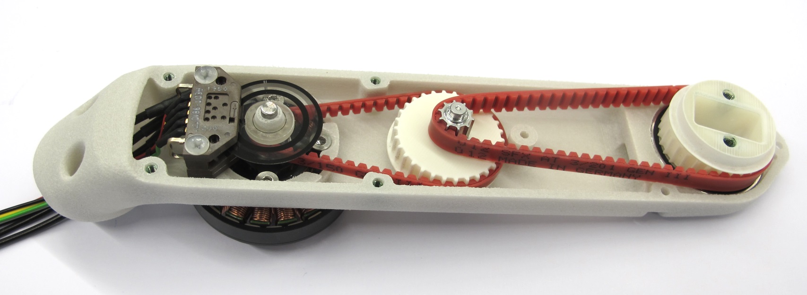
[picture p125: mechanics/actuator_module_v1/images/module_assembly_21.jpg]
 <br>*The base of the actuator module is now completed.*

### Installing the Timing Belt Tensioner Rollers

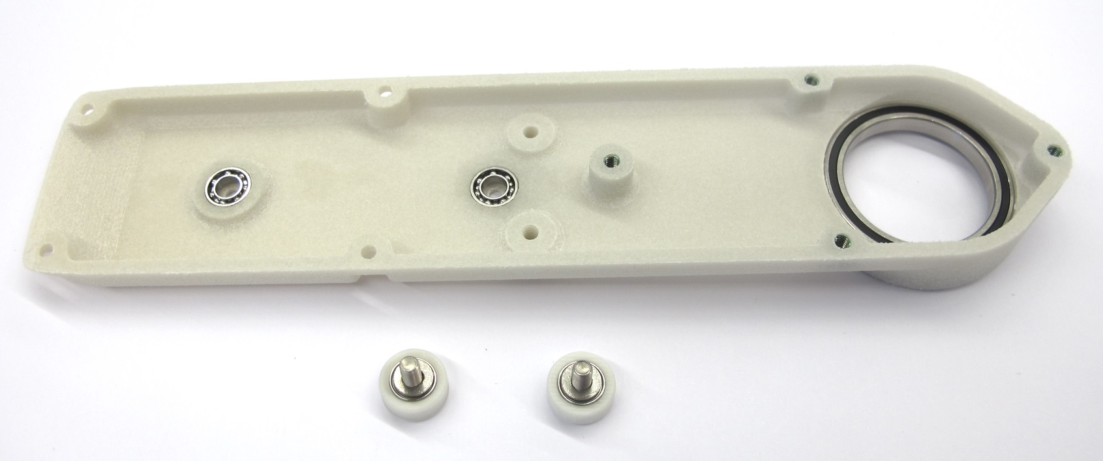
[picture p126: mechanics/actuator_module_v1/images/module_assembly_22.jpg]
 <br>*For this step you will need the shell cover and the timing belt tensioner rollers.*

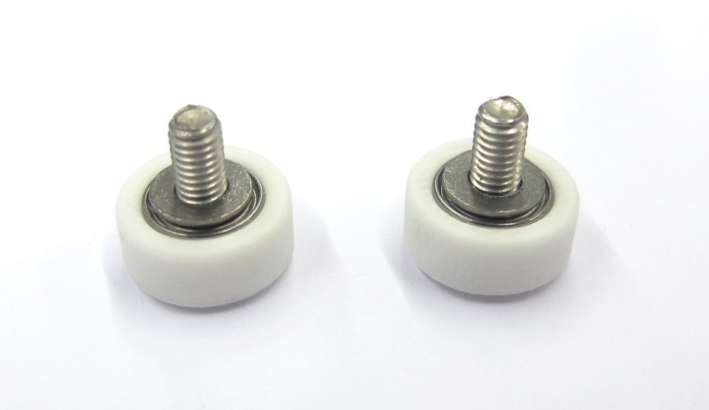
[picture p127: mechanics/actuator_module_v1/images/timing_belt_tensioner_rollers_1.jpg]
 <br>*Make sure that the washers are installed.*

 <br>*Install the timing belt tensioner rollers using a 2mm hex driver.<br> Rotate the rollers and make sure that they move freely.*

 <br>*All the components are installed - the shell can now be closed.*

### Closing the Shell

 <br>*Place the shell cover on the shell base.<br>Angle the cover a bit and partially install the output pulley as shown above.*

 <br>*Apply moderate pressure to the center of the assembly for all the following steps.*

 <br>*You will now need to push the timing belt of the second stage inwards.<br>That helps the timing belt to clear the tensioner rollers.*

 <br>*Use a small flat head screw driver to push the timing belt inwards.<br>Keep applying moderate pressure while turning the assembly around.*

 <br>*Use a small flat head screw driver to push the timing belt inwards on the opposite side.<br>The cover should move downwards a bit when the timing belt clears the roller.*

 <br>*Now the center pulley needs to find its way into the bearing on the cover.<br>Grab the rotor and rotate it back and forth a couple of times while gently pushing down on the cover.*

 <br>*The cover should close after a couple of turns in each direction.<br>Make sure that the shell is fully closed and that the motor can be rotated.*

 <br>*If you have trouble closing the shell you can use a pointed tool to guide the center pulley into the bearing.<br>There is a hole in the center pulley for that purpose.*

 <br>*Use a pointed tool to push the center pully into the direction of the motor.<br>Turning the rotor at the same time can help.*

 <br>*When the shell is fully closed the fasteners can be installed.*

 <br>*Use a 2mm hex driver to install the eight connecting screws.<br>Tighten the screws with moderate torque.<br>The location of the screws is documented below.*

 <br>*Fasteners for connecting the Actuator Module Assembly<br>SHCS = Socket Head Cap Screw*

 <br>*The actuator module is now fully assembled.<br>The last step is to add the motor phase and encoder connectors.*

### Soldering the Motor Phase Connectors

 <br>*[Instructions Soldering the Motor Phase Connectors](details_motor_preparation.md#soldering-the-motor-phase-connectors)*

### Crimping the Encoder Connector

 <br>*[Instructions Crimping the Encoder Connectors](details_encoder_preparation.md#crimping-hirose-connector)*

 <br>*The actuator module assembly is now completed.<br>The next step is to test the module and determine the correct order of the motor phases.<br>Weight of the actuator module with 30cm wires: 160g*

---
## Step-by-Step Instructions

| Motor Preparation  | Motor Shaft Preparation | Encoder Preparation |Center Pulley Preparation|
| --- | --- | --- | --- |
| |   |   | |

| Output Pulley Preparation | Shell Preparation | Actuator Module Assembly |Actuator Module Testing|
| --- | --- | --- | --- |
| |   |   | |

---
## More Details
| Details 3d Printed Parts | Details Machined Parts | Mechanical Tools and Consumables |Electronic Components and Tools|
| --- | --- | --- | --- |
|||||

---
## More Information
[Open Dynamic Robot Initiative - Webpage](https://open-dynamic-robot-initiative.github.io)  
[Open Dynamic Robot Initiative - YouTube Channel](https://www.youtube.com/channel/UCx32JW2oIrax47Gjq8zNI-w)   
[Open Dynamic Robot Initiative - Forum](https://odri.discourse.group/categories)  
[Open Dynamic Robot Initiative - Paper](https://arxiv.org/pdf/1910.00093.pdf)  
[Hardware Overview](../../../README.md#open-robot-actuator-hardware)  
[Software Overview](https://github.com/open-dynamic-robot-initiative/open-dynamic-robot-initiative.github.io/wiki)  
[Back to Actuator Module](../README.md)  
[Back to Top of Page](#details-actuator-module-assembly)

---
## Authors
Felix Grimminger

## License
BSD 3-Clause License

## Copyright
Copyright (c) 2019-2020, Max Planck Gesellschaft and New York University

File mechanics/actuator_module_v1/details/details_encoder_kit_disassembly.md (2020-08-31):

# Details Encoder Kit Disassembly
 <br>*Encoder Kit with AEDT 9810 encoder and 5000cpr codewheel.*  

## Description
 <br>*Use a thin screwdriver to undo the snap fit connection between the casing and the cover.*  

 <br>*Same thing on the other side.   
Once both sides are released the cover can be pulled of or pried out. <br> Be careful not to scratch the encoder disc.*

 <br>*Open encoder case.*

 <br>*Remove the encoder carefully using the screwdriver as a lever.<br> The encoder is connected by a light press fit.<br> There is a notch at the bottom of the encoder that can be used.*

 <br>*Carefully take the encoder and code wheel out of the casing.*

 <br>*The aluminum collar on the code wheel has to be removed on a lathe.<br> Cover the optical disc with tape to protect from scratching.*

Modify the aluminium flange according to [this drawing](../drawings/codewheel_modification.PDF)

---
## Step-by-Step Instructions

| Motor Preparation  | Motor Shaft Preparation | Encoder Preparation |Center Pulley Preparation|
| --- | --- | --- | --- |
| |   |   | |

| Output Pulley Preparation | Shell Preparation | Actuator Module Assembly |Actuator Module Testing|
| --- | --- | --- | --- |
| |   |   | |

---
## More Details
| Details 3d Printed Parts | Details Machined Parts | Mechanical Tools and Consumables |Electronic Components and Tools|
| --- | --- | --- | --- |
|||||

---
## More Information
[Open Dynamic Robot Initiative - Webpage](https://open-dynamic-robot-initiative.github.io)  
[Open Dynamic Robot Initiative - YouTube Channel](https://www.youtube.com/channel/UCx32JW2oIrax47Gjq8zNI-w)   
[Open Dynamic Robot Initiative - Forum](https://odri.discourse.group/categories)  
[Open Dynamic Robot Initiative - Paper](https://arxiv.org/pdf/1910.00093.pdf)  
[Hardware Overview](../../../README.md#open-robot-actuator-hardware)  
[Software Overview](https://github.com/open-dynamic-robot-initiative/open-dynamic-robot-initiative.github.io/wiki)  
[Back to Actuator Module](../README.md)  
[Back to Details Encoder](details_encoder.md)
[Back to Top of Page](#details-encoder-kit-disassembly)

---
## Authors
Felix Grimminger

## License
BSD 3-Clause License

## Copyright
Copyright (c) 2019-2020, Max Planck Gesellschaft and New York University

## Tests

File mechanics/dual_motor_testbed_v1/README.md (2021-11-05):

# Dual Motor Testbed v1

 <br>*Dual Motor Testbed consisting of two motors, two encoders and 3d printed parts*

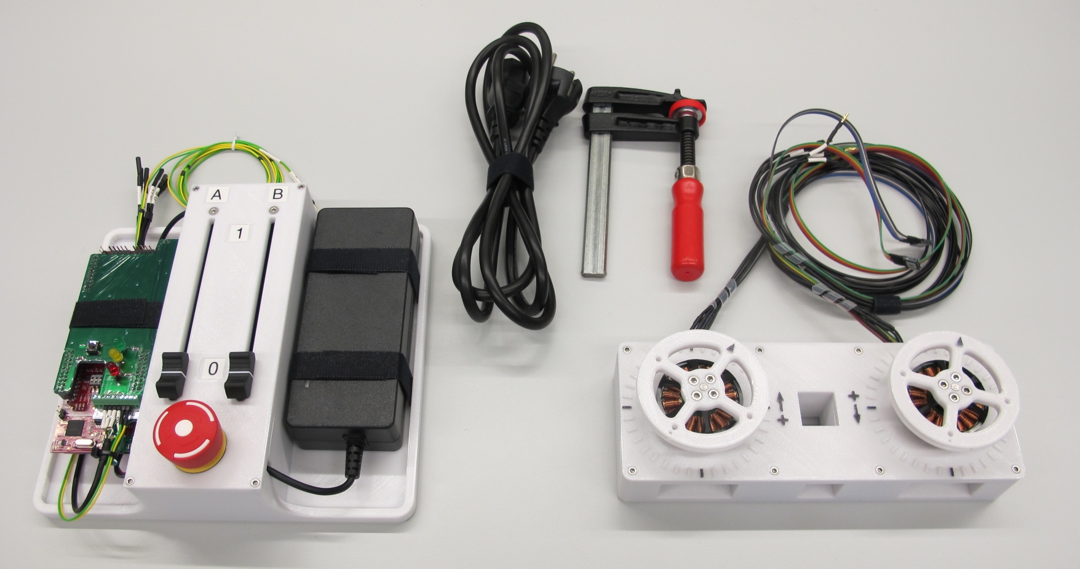
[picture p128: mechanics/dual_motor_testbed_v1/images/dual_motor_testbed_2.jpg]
 <br>*Dual Motor Testbed with Dual Motor Electronics Box*

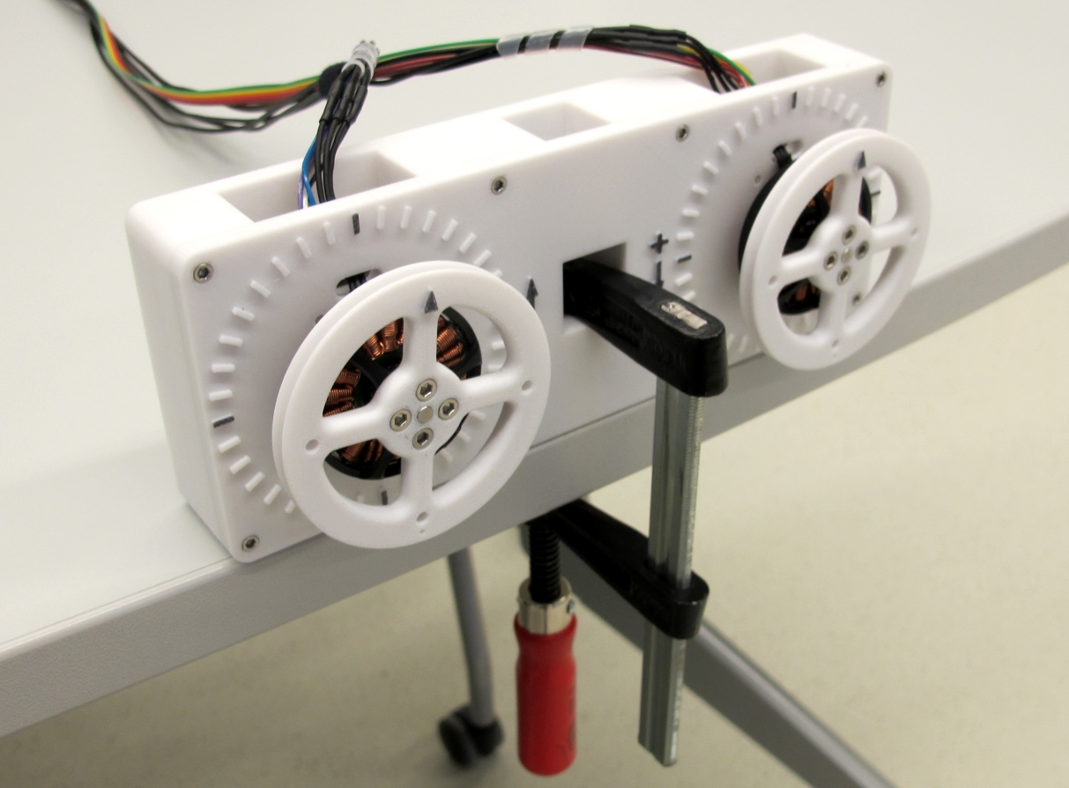
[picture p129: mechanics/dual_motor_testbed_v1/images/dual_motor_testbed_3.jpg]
 <br>*The testbed can be clamped to the table for experiments*

## Description
* this is the simplest mechanical setup to get started with brushless motor torque control
* the testbench consists of two brushless motors and two high resolution encoders mounted directly onto the motor shaft
* the encoders are required for the precise commutation of the motors using field oriented control
* in contrast to "sensorless" control (which the Texas Instruments boards also support) the torque control also works at slow speeds and when the motor is stalled

## Off-the-shelf Components

### Brushless DC Motor

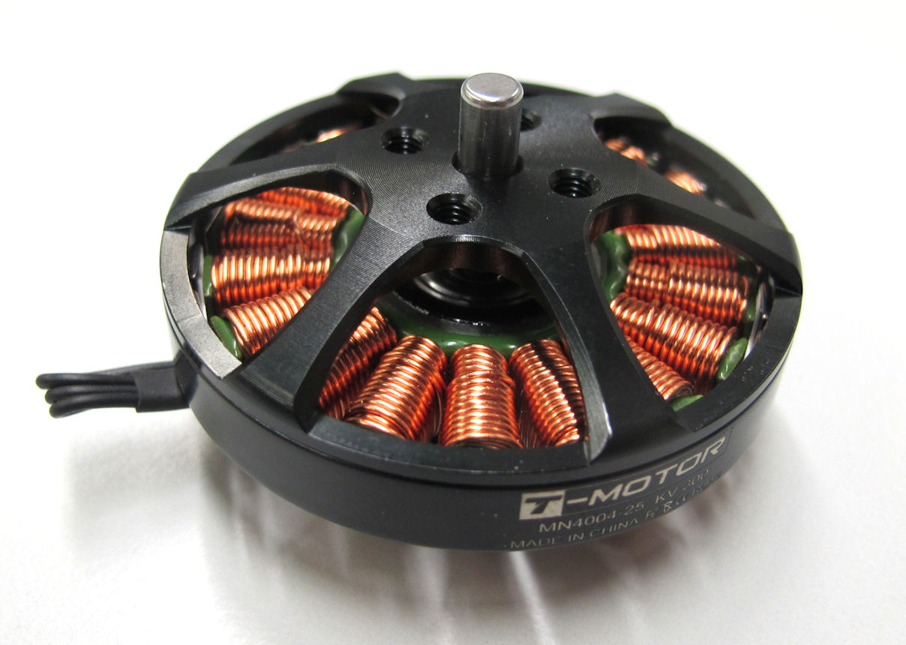
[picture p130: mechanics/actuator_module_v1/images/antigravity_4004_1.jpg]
 <br>

  * T-Motor Antigravity 4004 300kV
  * 24 magnets / 12 pole pairs / 18 slots
  * 3 phase WYE Configuration / Star Configuration
  * Rotor diameter: 45mm
  * Weight: 53g
  * the Antigravity motors are sold in sets of two pieces
  * [T-Motor Webpage](http://store-en.tmotor.com/goods.php?id=438)

### Optical Encoder
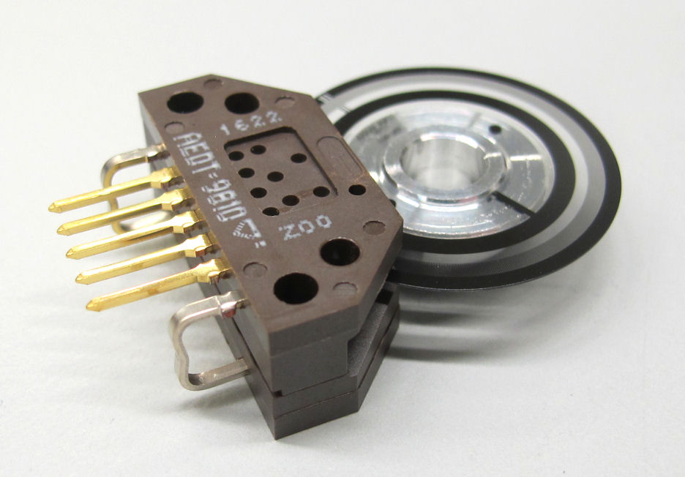
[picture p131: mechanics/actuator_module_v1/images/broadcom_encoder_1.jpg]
 <br>
  * Broadcom Encoder Kit AEDM-5810-Z12 consisting of the AEDT-9810-Z00 encoder and the high resolution code wheel with index
  * 5000 pulses per revolution per channel
  * 5V two channel quadrature output with index pulse (ABZ)
  * Code wheel diameter: 26mm
  * Weight: 5g  
  * Instructions on how to extract the encoder and the code wheel from the kit can be found here: [Instructions Encoder Kit Disassembly](../actuator_module_v1/details/details_encoder_kit_disassembly.md)
  * [Broadcom Encoder AEDT-9810-Z00 Webpage](https://www.broadcom.com/products/motion-control-encoders/incremental-encoders/transmissive-encoders/aedt-981x)  

## Machined Parts

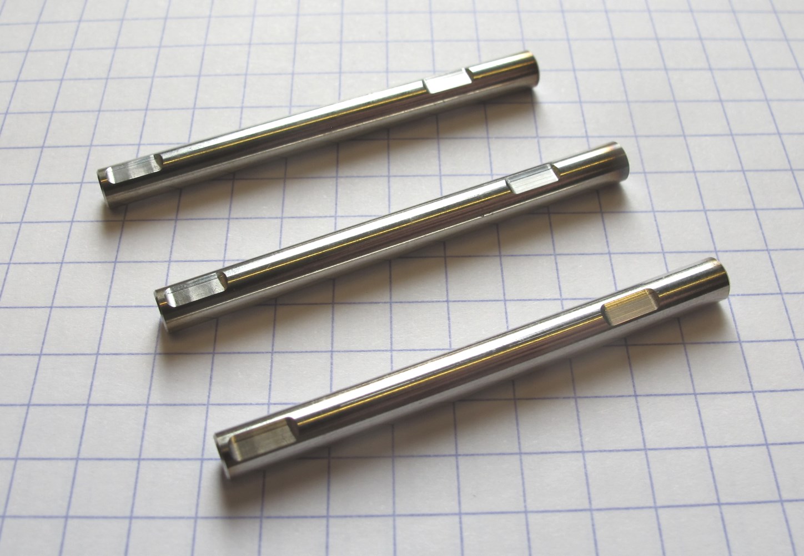
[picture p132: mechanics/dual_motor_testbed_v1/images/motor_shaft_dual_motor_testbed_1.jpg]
 <br>*Custom motor shaft made from stainless steel*    
* for attaching the codewheel the original motor shaft has to be replaced by this custom motor shaft
* Instructions on how to replace the original motor shaft can be found here: [Instructions Motor Preparation](../actuator_module_v1/details/details_motor_preparation.md)

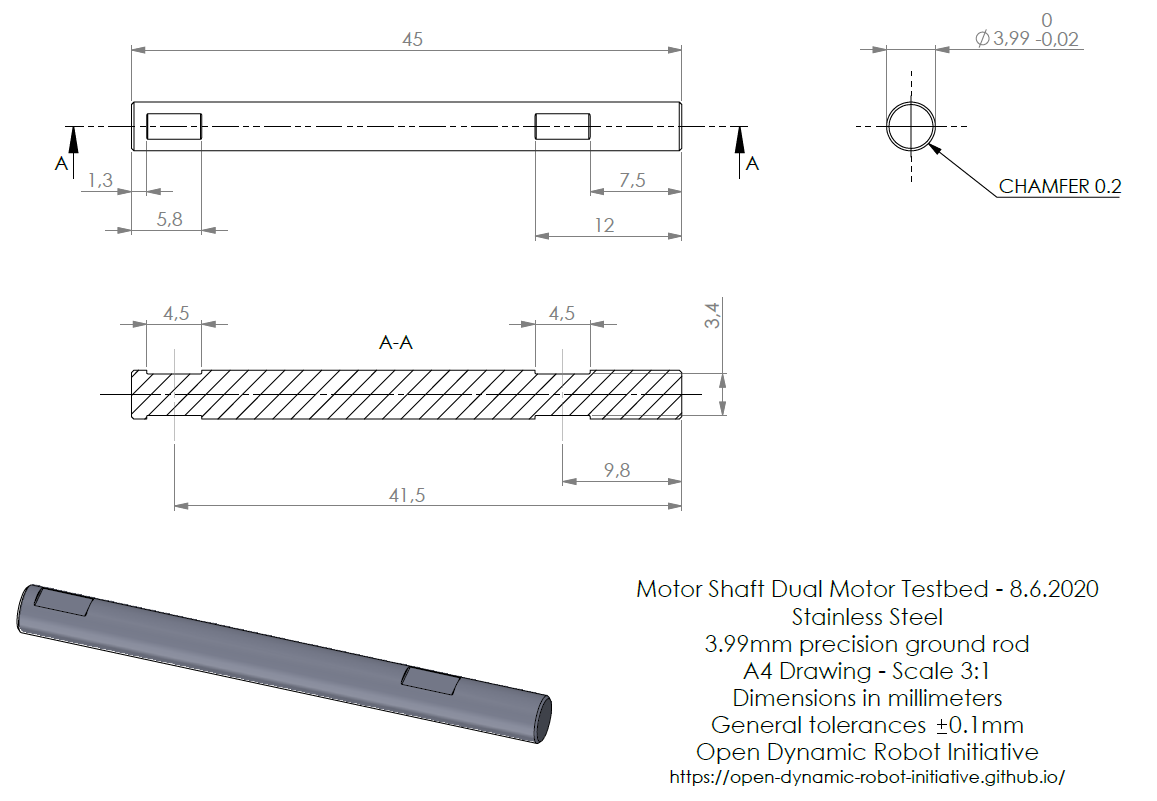
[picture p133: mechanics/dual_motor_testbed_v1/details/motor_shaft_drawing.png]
<br>*Click on picture above to view the PDF drawing*

## 3D Printed Parts

 <br>

`The recommended printing direction for all the parts below is the positive z direction of the stl files.`

---
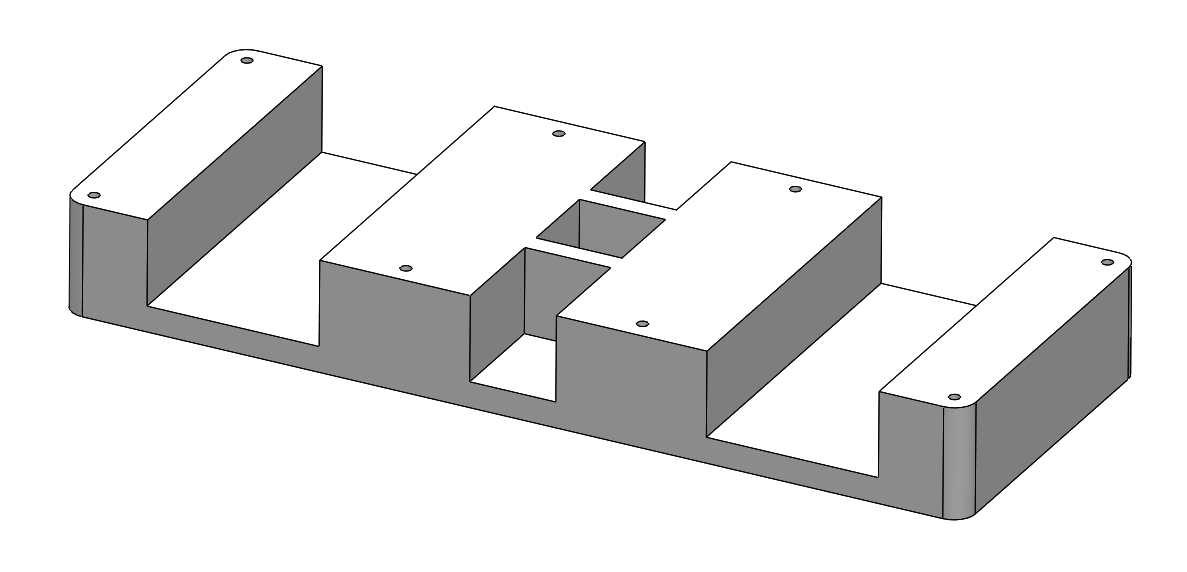
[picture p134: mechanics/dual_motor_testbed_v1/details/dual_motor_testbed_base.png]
 <br>
* [Dual Motor Testbed Base - STL file](stl_files/dual_motor_testbed_base.STL)<br>
* we print this part with the "sparse double dense" printer setting
* that saves material and print time
* the recommended printing direction is the positive z direction of the stl file
---
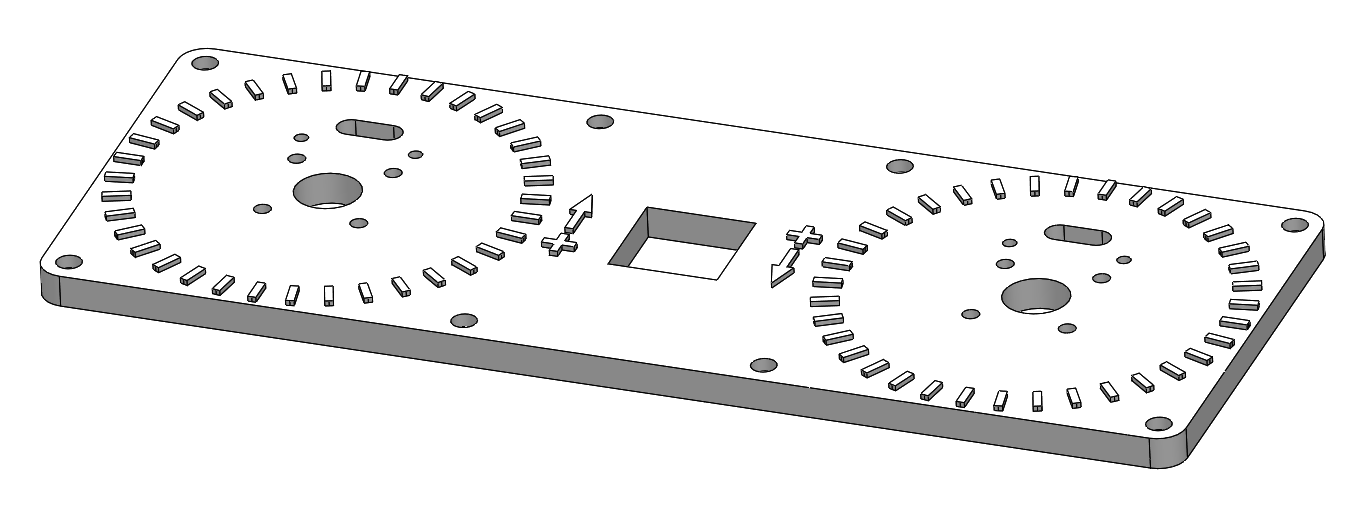
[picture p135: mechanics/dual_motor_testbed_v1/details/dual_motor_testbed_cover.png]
 <br>
* [Dual Motor Testbed Cover - STL file](stl_files/dual_motor_testbed_cover.STL)<br>
* the recommended printing direction is the positive z direction of the stl file
---
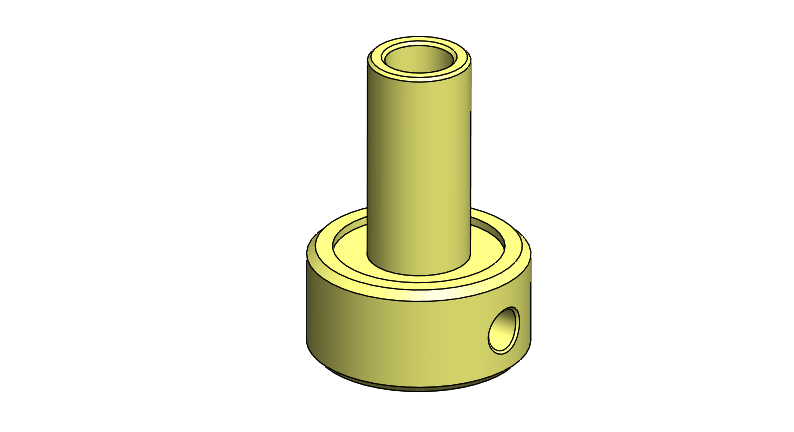
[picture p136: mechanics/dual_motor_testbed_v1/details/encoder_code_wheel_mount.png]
 <br>
* [Encoder Code Wheel Mount - STL file](stl_files/encoder_code_wheel_mount.STL)<br>
* the recommended printing direction is the positive z direction of the stl file
---
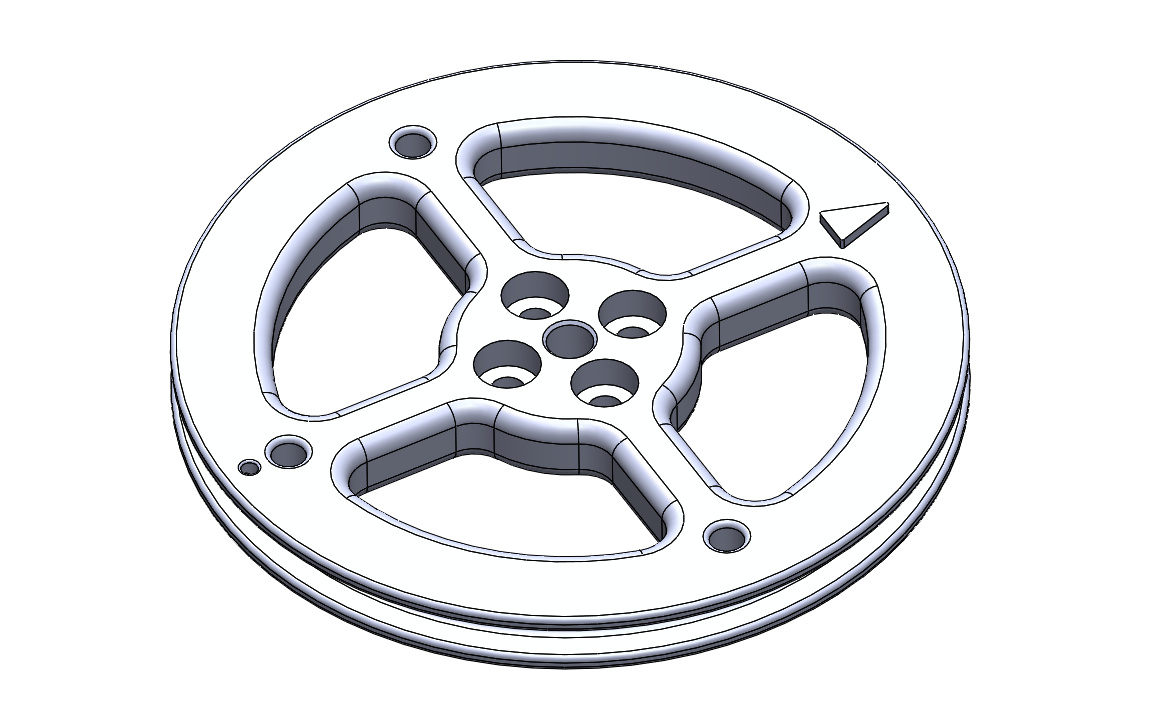
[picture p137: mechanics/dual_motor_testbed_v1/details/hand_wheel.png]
 <br>
* [Hand Wheel - STL file](stl_files/hand_wheel.STL)<br>
* the recommended printing direction is the positive z direction of the stl file

# Bill of Materials - Dual Motor Testbed


| Part Name | Quantity | Ordering Information | Comments |  
| --- | --- | --- | --- |
| Brushless Motor | 2 | T-Motor Antigravity 4004 300kV | Sold in set of two pieces |  
| Optical Encoder with Codewheel | 2 | Broadcom Encoder Kit AEDM-5810-Z12<br>Digi-Key 516-3253-ND |[Encoder Kit Disassembly Instructions](../actuator_module_v1/details/details_encoder_kit_disassembly.md#details-encoder-kit-disassembly) | 
| Custom Motor Shaft | 2 | [PDF Drawing](details/motor_antigravity_4004_custom_shaft.PDF) | Machined part |  
| Testbed Base | 1 | [STL file](stl_files/dual_motor_testbed_base.STL) | 3d printed part |
| Testbed Cover | 1 | [STL file](stl_files/dual_motor_testbed_cover.STL) | 3d printed part |
| Code Wheel Mount | 2 | [STL file](stl_files/encoder_code_wheel_mount.STL) | 3d printed part |
| Hand Wheel | 2 | [STL file](stl_files/hand_wheel.STL) | 3d printed part |
| Rubber Feet | 6 | RS 236-509 | Optional |
| Fasteners Stator and Hand Wheel | 16 | Socket Head Cap Screw M3x6 | Stainless steel |
| Fasteners Testbed Cover | 8 | Socket Head Cap Screw M2,5x8 | Stainless steel |
| Fasteners Code Wheel Mount | 4 | Set Screw M3x4 | Stainless steel |
| Fasteners Encoder | 4 | Flat Head Phillips Screw M3x16<br>Conrad 839967 | Nylon |

# Dual Motor Electronics Box
 <br>*Dual Motor Electronics Box*

## Off-the-shelf Components

### Texas Instruments Dual Motor Evaluation Boards

 <br>*Texas Instruments dual motor control electronics stack*

 <br>*Components dual motor control electronics stack*
* 1 x Microcontroller: TI Launchpad F28069M -> [Launchpad Product Page](http://www.ti.com/tool/LAUNCHXL-F28069M)
* 2 x Motor Driver Card: TI Boosterpacks DRV8305  -> [Booster Pack Product Page](http://www.ti.com/tool/BOOSTXL-DRV8305EVM)

### Analog Linear Potentiometers
 <br>  
* Linear potentiometer 10 kohm
* Alps Alpine RSA0K12B1019

### E-Stop Switch
 <br>  
* E-stop switch 32mm
* Pilz 84-5040.0040

### Power Supply
 <br>  
* Power Supply 24V
* Meanwell GST90A24

### CAN Card
 <br>  
* PEAK PCAN PCI Express Card
* dual channel - galvanically  isolated

### CAN Connector
 <br>
* 9 pole D-Sub connector

## 3D Printed Parts
 <br>
* [Dual Motor Electronics Box Base - STL file](stl_files/electronics_box_base.STL)<br>
* the recommended printing direction is the positive z direction of the stl file
---
 <br>
* [Dual Motor Electronics Box Cover - STL file](stl_files/electronics_box_cover.STL)<br>
* the recommended printing direction is the positive z direction of the stl file

# Bill of Materials - Dual Motor Electronics Box


| Part Name | Quantity | Ordering Information | Comments |  
| --- | --- | --- | --- |
| Texas Instruments Microcontroller | 1 | TI Launchpad F28069M <br >Digi-Key 296-38832-ND| [Launchpad Product Page](http://www.ti.com/tool/LAUNCHXL-F28069M) |  
| Texas Instruments Motor Driver Electronics  | 2 |  TI Boosterpack DRV8305EVM <br >Digi-Key 296-43181-ND | [Booster Pack Product Page](http://www.ti.com/tool/BOOSTXL-DRV8305EVM) |
| Linear Potentiometer | 2 | Alps Alpine RSA0K12B1019<br>RS 234-6544 |  |
| Linear Potentiometer Knob | 2 | RS 281-7197 |  |
| E-Stop Switch | 1 | Pilz 	84-5040.0040 <br> RS 690-6954 |  |
| Power Supply 24V | 1 | Meanwell GST90A24<br> RS 880-8427 |  |
| Electronics Box Base | 1 | [STL file](stl_files/electronics_box_base.STL) | 3d printed part |
| Electronics Box Cover | 1 | [STL file](stl_files/electronics_box_cover.STL) | 3d printed part |
| Fasteners Linear Potentiometer | 4 | Flat Head Screw M3x10 | Stainless steel |
| Fasteners Electronics Box Cover | 4 | Socket Head Cap Screw M2,5x8 | Stainless steel |
| Rubber Feet | 6 | RS 236-509 | Optional |
| CAN PCI Express Card | 1 | PEAK IPEH-003027 | Dual channel |
| CAN Connector | 1 | 9 pole D-Sub connector<br>RS 765-9555 |  |

## View the dual motor testbed cad model in your web browser
<br>

<br> *Dual Motor Testbed - Click on the picture to view the cad model in your browser*

## CAD Files

The Solidworks CAD files are available here: [Dual Motor Testbed v1 Solidworks CAD files](solidworks_files/dual_motor_testbed_v1.zip)

## More Information
[Open Dynamic Robot Initiative - Webpage](https://open-dynamic-robot-initiative.github.io)  
[Open Dynamic Robot Initiative - YouTube Channel](https://www.youtube.com/channel/UCx32JW2oIrax47Gjq8zNI-w)   
[Open Dynamic Robot Initiative - Forum](https://odri.discourse.group/categories)  
[Open Dynamic Robot Initiative - Paper](https://arxiv.org/pdf/1910.00093.pdf)  
[Hardware Overview](../../README.md#open-robot-actuator-hardware)  
[Software Overview](https://github.com/open-dynamic-robot-initiative/open-dynamic-robot-initiative.github.io/wiki)

## Authors
Felix Grimminger

## License
BSD 3-Clause License

## Copyright
Copyright (c) 2019-2021, Max Planck Gesellschaft and New York University

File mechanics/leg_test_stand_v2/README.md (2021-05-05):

# Leg Test Stand v2
 <br>  

## Description

This teststand allows us to evaluate the performance of a single 2dof leg with external sensors.
The teststand has a linear guided vertical degree of freedom and a carriage that holds the leg and the motor driver electronics. The ground reaction forces are measured with a 6 axis force-torque-sensor and are transmitted to the control pc at 1kHz. The vertical position of the carriage is measured with an analog string potentiometer. The test stand can be equipped with a pull-up-motor module for automated resetting to the initial position for machine learning experiments.

* This is an updated version of the [Leg Test Stand v1](../leg_test_stand_v1#leg-test-stand-v1)
* The details of the 2dof leg are described here: [Leg 2dof v2](../leg_2dof_v2/README.md#leg-2dof-v2)
* the details of the custom electronics are described here:
  * [Details Master Board](https://github.com/open-dynamic-robot-initiative/master-board#master-board)
  * [Details Micro Driver Board](../../electronics/micro_driver_electronics/README.md#micro-driver-electronics)

## Details Leg Test Stand

 <br>*Leg Test Stand v2 cad model*<br>

* vertical range: 85cm
* pull-force height sensor about 2N
* weight carriage with electronics and 2dof leg: 713g
* 24V power supply and ethernet connection

 <br>*Carriage with 2dof leg and custom motor driver electronics  - weight: 713g*<br>

## Electronics

 <br> *Electronics Stack - weight: 45g*

### Master Board
 <br> *Master Board v2 - weight: 19g each*
* [Master Board Documentation](https://github.com/open-dynamic-robot-initiative/master-board#master-board)

### Micro Driver Electronics
 <br> *Micro Driver Electronics - weight: 13g*

* the micro driver board controls 2 brushless motors
* [Micro Driver Board Documentation](../../electronics/micro_driver_electronics/README.md#micro-driver-electronics)

### Height Sensor
<br>*Waycon string potentiometer*<br>

* Waycon LX-PA-40 string potentiometer
* measurement range 1000mm
* [Waycon Webpage](https://www.waycon.biz)
* [Waycon String Potentiometer Datasheet](https://www.waycon.biz/fileadmin/draw-wire-sensors/Draw-Wire-Sensor-LX.pdf)
* ordering information [below](#bill-of-materials---leg-test-stand-v2)

### Force Torque Sensor
 <br>*ATI Mini-40-E force-torque-sensor*<br>
* 6 axis force-torque sensor
* ATI Mini-40-E with SI-40-2 Calibration
* NetBA Interface Box required
* Ethernet communication with control pc
* [ATI Mini-40 Product Page](https://www.ati-ia.com/products/ft/ft_models.aspx?id=Mini40)
* [ATI Mini-40-E Technical Drawing](https://www.ati-ia.com/app_content/Documents/9230-05-1314.auto.pdf)
* [NetBA Interface Box Technical Drawing](https://www.ati-ia.com/app_content/documents/9230-05-1327.auto.pdf)
* ordering information [below](#bill-of-materials---leg-test-stand-v2)

## Off-the-shelf Components
### Linear Guide
 <br>*Linear ball bearing and linear motion rod*<br>

* Linear ball bearings: KB-1
* Rod diameter 14mm
* Linear motion rods: Precision Stainless Steel Rods X46 14h6 x 1000mm
* ordering information [below](#bill-of-materials---leg-test-stand-v2)

### Aluminum profiles
 <br> *Item aluminum profile*<br>
* Item aluminum profiles - Size 8 - 40mm x 40mm
* required profile length: 2,7m
* segment lengths: 120cm / 70cm / 50cm / 30cm
* ordering information [below](#bill-of-materials---leg-test-stand-v2)

### Angle brackets
 <br> *Item 90 degree angle bracket 40mm*<br>
* 90 degree 40mm angle brackets
* ordering information [below](#bill-of-materials---leg-test-stand-v2)

### End caps
 <br> *Item end caps*<br>
* end caps - size 8
* ordering information [below](#bill-of-materials---leg-test-stand-v2)

### T-slot nuts
 <br> *Item M5 t-slot nuts*<br>
* T-slot nuts M5
* ordering information [below](#bill-of-materials---leg-test-stand-v2)

### Steel Pins
 <br> *5mm Steel Pins*<br>
* Steel Pins - 5mm x 28mm
* ordering information [below](#bill-of-materials---leg-test-stand-v2)

### Carbon-Fiber Tube
 <br> *Carbon-fiber tube*<br>
* O.D. 6mm / I.D. 4mm / Length 30cm
* for wire management
* ordering information [below](#bill-of-materials---leg-test-stand-v2)

---
## 3D Printed Parts

 <br>

`The recommended printing direction for all the parts below is the positive z direction of the stl files.`

All the STL files for 3d printing the Leg Test Stand can be found here: [STL Files Leg Test Stand](stl_files).

---
 <br>
* [Carriage - STL file](stl_files/carriage.STL)
* print on FDM or SLS printer
---
 <br>
* [Master Board Support - STL file](stl_files/master_board_support.STL)
* print on FDM or SLS printer
---
 <br>
* [Spacer Micro Driver Stack - STL file](stl_files/spacer_micro_driver_stack.STL)
* print on SLA, Multijet or Polyjet printer
---
 <br>
* [Linear Bearing Cover - STL file](stl_files/linear_bearing_cover.STL)
* print on FDM or SLS printer
---
 <br>
* [Adjustment Sleeve - STL file](stl_files/adjustment_sleeve.STL)
* print on SLA, Multijet or Polyjet printer
---
 <br>
* [Linear Motion Rod Attachment - STL file](stl_files/linear_motion_rod_attachment.STL)
* print on FDM or SLS printer
---
 <br>
* [String Potentiometer and Pullup Motor Mount - STL file](stl_files/string_potentiometer_pullup_motor_mount.STL)
* print on FDM or SLS printer
---
 <br>
* [Pulley Pullup Module - STL file](stl_files/pulley_pull_up_module.STL)
* for pullup motor / optional
* print on FDM or SLS printer
---
 <br>
* [ATI Sensor Top Plate - STL file](stl_files/ati_sensor_top_plate.STL)
* print on FDM or SLS printer
---
 <br>
* [ATI Sensor Bottom Plate - STL file](stl_files/ati_sensor_bottom_plate.STL)
* print on FDM or SLS printer
---
 <br>
* [Motor Driver Electronics Attachment - STL file](stl_files/motor_driver_electronics_attachment.STL)
* for pullup motor electronics / optional
* print on FDM or SLS printer
---
 <br>
* [Stopper Attachment - STL file](stl_files/stopper_attachment.STL)<br>
* print on FDM or SLS printer
---
 <br>
* [Stopper Wing - STL file](stl_files/stopper_wing.STL)<br>
* print on FDM or SLS printer
---

## Bill of Materials - Leg Test Stand v2
 <br>

| Description | Quantity | Ordering Information | Comments |  
| --- | --- | --- | --- |
|2DOF Leg |1|[2DOF Leg Documentation](../leg_2dof_v2/README.md#leg-2dof-v2)|Custom assembly|
|Master Board|1|[Master Board Documentation](https://github.com/open-dynamic-robot-initiative/master-board#master-board)|Custom electronics|
|Micro Driver Board|1|[Micro Driver Board Documentation](../../electronics/micro_driver_electronics/README.md#micro-driver-electronics)|Custom electronics|
|String Potentiometer|1|Waycon LX-PA-40<br>[Waycon Distributors](https://www.waycon.biz/distributors/europe/)|1000mm measurement range<br>[Waycon String Potentiometer Datasheet](https://www.waycon.biz/fileadmin/draw-wire-sensors/Draw-Wire-Sensor-LX.pdf)|
|6 Axis Force-Torque-Sensor|1|ATI Mini-40-E<br>SI-40-2 calibration<br>[ATI Sales](https://www.ati-ia.com/company/contacts.aspx)|[ATI Mini-40 Product Page](https://www.ati-ia.com/products/ft/ft_models.aspx?id=Mini40)<br>We ordered the sensor and interface box from [Schunk](https://schunk.com/de_en/gripping-systems/product/30836-ftn-mini-40-si-40-2/) in Germany.|
|Inertia Measurement Unit|1|Lord Microstrain 3DM-GX5-25 AHRS<br>[Lord Microstrain Distributors](https://www.microstrain.com/support/distributors)| [3DM-GX5-25 AHRS Datasheet](https://www.microstrain.com/sites/default/files/3dm-gx5-25_datasheet_8400-0093_rev_o.pdf)<br>We ordered the IMU from [ZSE Electronic GmbH](https://www.zse.de/en/) in Germany.|
|Linear Ball Bearings|4|KB-1 14mm<br>[Mädler 64699814](https://www.maedler.de/product/1643/1630/2358/linearkugellager-kb-1-iso-serie-1-rostfrei-mit-deckscheiben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)||
|Linear Motion Rods|2|Precision Stainless Steel Rods X46 14h6 x 1000mm<br>[Mädler 64799214](https://www.maedler.de/product/1643/1630/559/praezisions-wellenstahl-edelstahl-x46-rostfrei-gehaertet-und-geschliffen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)||
|Aluminum Profiles|4|Item Size 8 - 40mm x 40mm <br>[Item 7.0.000.09](https://product.item24.de/en/products/product-catalogue/productdetails/products/line-8-construction-profiles-1001042794/profile-8-40x40-e-natural-7000009/)|Segment lengths: 120cm / 70cm / 30cm / 50cm|
|Angle Brackets|4|[Item 0.0.411.15](https://product.item24.de/en/products/product-catalogue/productdetails/products/angle-brackets-zn-1001046547/angle-bracket-set-8-40x40-41115/)|Bolts and nuts included.|
|End Caps|5|[Item 0.0.026.01](https://product.item24.de/en/products/product-catalogue/productdetails/products/caps-for-profiles-in-modular-dimensions-1001042804/cap-8-40x40-black-2601/)||
|T-Slot Nuts M5|7|[Item 0.0.480.54](https://product.item24.de/en/products/product-catalogue/productdetails/products/t-slot-nuts-st-1001042830/t-slot-nut-v-8-st-m5-bright-zinc-plated-48054/)||
|Steel Pin 5mm x 28mm|2|||
|Carbon-fiber tube 6mm|1|[R&G 7406041](https://shop1.r-g.de/en/art/740908)|Length 30cm|
|Carriage|1|[STL file](stl_files/carriage.STL)|3d printed part<br>Print on FDM or SLS printer.|
|Master Board Support|1|[STL file](stl_files/master_board_support.STL)|3d printed part<br>Print on FDM or SLS printer.|
|Spacer Micro Driver Stack|8|[STL file](stl_files/spacer_micro_driver_stack.STL)|3d printed part<br>Print on SLA, Polyjet or Multijet printer.|
|Linear Bearing Cover|4|[STL file](stl_files/linear_bearing_cover.STL)|3d printed part<br>Print on FDM or SLS printer.|
|Adjustment Sleeve|4|[STL file](stl_files/adjustment_sleeve.STL)|3d printed part<br>Print on SLA, Polyjet or Multijet printer.|
|Linear Motion Rod Attachment|2|[STL file](stl_files/linear_motion_rod_attachment.STL)|3d printed part<br>Print on FDM or SLS printer.|
|String Potentiometer and Pullup Motor Mount|1|[STL file](stl_files/string_potentiometer_pullup_motor_mount.STL)|3d printed part<br>Print on FDM or SLS printer.|
|Pulley Pullup Module|1|[STL file](stl_files/pulley_pull_up_module.STL)|3d printed part / optional<br>Print on FDM or SLS printer.|
|ATI Sensor Top Plate|1|[STL file](stl_files/ati_sensor_top_plate.STL)|3d printed part<br>Print on FDM or SLS printer.|
|ATI Sensor Bottom Plate|1|[STL file](stl_files/ati_sensor_bottom_plate.STL)|3d printed part<br>Print on FDM or SLS printer.|
|Motor Driver Electronics Attachment|1|[STL file](stl_files/motor_driver_electronics_attachment.STL)|3d printed part / optional<br>Print on FDM or SLS printer.|
|Stopper Attachment|2|[STL file](stl_files/stopper_attachment.STL)|3d printed part<br>Print on FDM or SLS printer.|
|Stopper Wing|1|[STL file](stl_files/stopper_wing.STL)|3d printed part<br>Print on FDM or SLS printer.|
|Carbon Fiber Rod|1||O.D. 5mm<br>I.D. 4mm<br>Length 30cm|
|Fasteners M3 x 8|16||Fasteners linear bearing covers|
|Fasteners M3 x 16|4||Fasteners 2dof leg|
|Fasteners M2,5 x 22|4||Fasteners electronics stack|
|Fasteners M2 x 5|4||Fasteners Master Board|

## Preparing the 3D Printed Parts

<br>

<br>

<br>

<br>

<br>

<br>

## View the Teststand Cad Model in your Web Browser
<br> *Leg Test Stand v2 - Click on the picture to view the cad model in your browser* <br>

* You can download the Solidworks CAD files [here](solidworks_files/leg_test_stand_v2.zip).

## More Information
[Open Dynamic Robot Initiative - Webpage](https://open-dynamic-robot-initiative.github.io)  
[Open Dynamic Robot Initiative - YouTube Channel](https://www.youtube.com/channel/UCx32JW2oIrax47Gjq8zNI-w)   
[Open Dynamic Robot Initiative - Forum](https://odri.discourse.group/categories)  
[Open Dynamic Robot Initiative - Paper](https://arxiv.org/pdf/1910.00093.pdf)  
[Hardware Overview](../../README.md#open-robot-actuator-hardware)  
[Software Overview](https://github.com/open-dynamic-robot-initiative/open-dynamic-robot-initiative.github.io/wiki)

## Authors
Felix Grimminger

## License
BSD 3-Clause License

## Copyright
Copyright (c) 2019-2021, Max Planck Gesellschaft and New York University

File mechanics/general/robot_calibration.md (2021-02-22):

# Robot Calibration
## Description


* when the robot is turned on the joint angles are unknown
* therefore we manually align the legs before startup such that the joints are roughly in zero position
* the software moves all the joints and finds the closest encoder index position for each joint
* when the index position is found the software adds an offset to the actual position and moves all the joints into zero position
* in order for this procedure to work the offsets between the index positions and the zero joint positions have to be measured and saved for each degree of freedom before once
* if an actuator module is repaired, replaced or modified the offset between the index pulse and the zero joint position has to be measured and saved again

## Calibration Tools


* we use 3d printed calibration tools to align the legs in the zero position
* this helps to determine the correct offsets from the index position for each joint
* steel pins that fit into the screw heads of the actuator modules are used to align the segments



---
## Calibration Tool Quadruped 8dof
<br>*8dof quadruped cad model with calibration tools.*<br>

* this calibration tool can be used for the [Quadruped Robot 8dof v1](../quadruped_robot_8dof_v1#quadruped-robot-8dof-v1) and the [Quadruped Robot 8dof v2](../quadruped_robot_8dof_v2#quadruped-robot-8dof-v2)

### Bill of Materials - Calibration Tool Quadruped 8dof


|Description|Quantity|Ordering Information|Comments|
|---|---|---|---|
|Calibration Tool Quadruped 8dof|2|[STL file](stl_files/calibration_tool_quadruped_8dof.STL)|3d printed part<br>We print this part with the "sparse double dense" setting on our FDM printer.|
|Calibration Tool Quadruped 8dof - Mirrored version|2|[STL file](stl_files/calibration_tool_quadruped_8dof_mirror.STL)|3d printed part<br>We print this part with the "sparse double dense" setting on our FDM printer.|
|Pin Spacer Tool 5mm|1|[STL file](stl_files/pin_spacer_5mm.STL)|3d printed tool|
|Pin 2mm x 16mm|8|[Online Schrauben](https://online-schrauben.de/shop/Stifte-ohne-Gewinde/DIN-7-Toleranzfeld-m6-Zylinderstifte-Toleranzfeld-m6-aehnl.-ISO-2338-Form-A/Edelstahl-Rostfrei-A1-1.4305/2,0-mm-Durchmesser)|Stainless Steel A1|
|Pin 2,5mm x 12mm|8|[Online Schrauben](https://online-schrauben.de/shop/Stifte-ohne-Gewinde/DIN-7-Toleranzfeld-m6-Zylinderstifte-Toleranzfeld-m6-aehnl.-ISO-2338-Form-A/Edelstahl-Rostfrei-A1-1.4305/2,5-mm-Durchmesser)|Stainless Steel A1|

### Preparing the Calibration Tools
<br>*Calibration tool - pin locations.*<br>

<br>*Use a 1,9mm drill bit to adjust the hole diameters for the 2mm pins.<br>Install the 2mm pins using a hammer.<br>The pins should protrude 5mm from the surface.<br>The [Pin Spacer Tool](stl_files/pin_spacer_5mm.STL) can help to position the pin correctly.*<br>

<br>*Use a 2,4mm drill bit to adjust the hole diameters for the 2,5mm pins.<br>Install the 2,5mm pins using a hammer.<br>*<br>

### Installing the Calibration Tools
<br>*Insert the pins into the screw heads of the actuator module and the lower leg.<br>Make sure that the tool is fully seated and that there is no gap between the parts.<br>We use velcro straps around the knee to keep the calibration tools in place.*<br>

---
## Calibration Tool Quadruped 12dof
<br>*12dof quadruped cad model with calibration tools.*<br>

* this calibration tool can be used for the [Quadruped Robot 12 dof  v1](../quadruped_robot_12dof_v1#quadruped-robot-12dof-v1)

### Bill of Materials - Calibration Tool Quadruped 12dof
<br>

|Description|Quantity|Ordering Information|Comments|
|---|---|---|---|
|Calibration Tool Quadruped 12dof v1|2|[STL file](stl_files/calibration_tool_quadruped_12dof_v1.STL)|3d printed part<br>We print this part with the "sparse double dense" setting on our FDM printer.|
|Calibration Tool Quadruped 12dof v1 - Mirrored version|2|[STL file](stl_files/calibration_tool_quadruped_12dof_v1_mirror.STL)|3d printed part<br>We print this part with the "sparse double dense" setting on our FDM printer.|
|Calibration Tool Quadruped 12dof v1 Connector|2|[STL file](stl_files/calibration_tool_quadruped_12dof_v1_connector.STL)|3d printed part|
|Pin Spacer Tool 4mm|1|[STL file](stl_files/pin_spacer_4mm.STL)|3d printed tool|
|Pin 2mm x 16mm|8|[Online Schrauben](https://online-schrauben.de/shop/Stifte-ohne-Gewinde/DIN-7-Toleranzfeld-m6-Zylinderstifte-Toleranzfeld-m6-aehnl.-ISO-2338-Form-A/Edelstahl-Rostfrei-A1-1.4305/2,0-mm-Durchmesser)|Stainless Steel A1|
|Pin 2,5mm x 12mm|8|[Online Schrauben](https://online-schrauben.de/shop/Stifte-ohne-Gewinde/DIN-7-Toleranzfeld-m6-Zylinderstifte-Toleranzfeld-m6-aehnl.-ISO-2338-Form-A/Edelstahl-Rostfrei-A1-1.4305/2,5-mm-Durchmesser)|Stainless Steel A1|
|Socket Head Cap Screw M3 x 16|8|[Online Schrauben](https://online-schrauben.de/shop/Schrauben/Innensechskantschrauben/ISO-4762-DIN-912-Zylinderkopfschrauben-mit-Innensechskant-aehnl.-DIN-912/Edelstahl-Rostfrei-A2/M-3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)|Stainless Steel A2|
|Threaded Inserts M3 x 4,5|8|[Hoffmann](https://www.hoffmann-group.com/US/en/hus/Power-tools-and-workshop-supplies/Soldering-tools-cleaning-devices-thread-repair/Thread-insert-set%2C-100-pieces-1-5×D/p/082818)<br>[McMaster](https://www.mcmaster.com/91732A647/)|Helicoil|

### Preparing the Calibration Tools
<br>*Calibration tool - pin locations.*<br>

<br>*Use a 1,9mm drill bit to adjust the hole diameters for the 2mm pins.<br>Install the 2mm pins using a hammer.<br>The pins should protrude 4mm from the surface.<br>The [Pin Spacer Tool](stl_files/pin_spacer_4mm.STL) can help to position the pin correctly.*<br>

<br>*Use a 2,4mm drill bit to adjust the hole diameters for the 2,5mm pins.<br>Install the 2,5mm pins using a hammer.<br>*<br>

<br>*Increase the square holes on the side of the connector in small steps.<br>Drill with 2,5mm / 2,7mm / 2,9mm and 3,1mm diameter.<br>Install M3x4,5 Helicoil threaded inserts in all four locations.*<br>

### Installing the Calibration Tools
<br>*Insert the pins into the screw heads of the actuator module and the lower leg.<br>Make sure that the tool is fully seated and that there is no gap between the parts.<br>We use velcro straps around the knees to keep the calibration tools in place.<br>Use M3x16 screws to install the connector part.*<br>

---
## Calibration Tool Biped 6dof
<br>*6dof biped cad model with calibration tool.*<br>

* this calibration tool can be used for the [Biped Robot 6 dof  v1](../biped_6dof_v1/README.md#biped-robot-6dof-v1)

### Bill of Materials - Calibration Tool Biped 6dof
<br>

|Description|Quantity|Ordering Information|Comments|
|---|---|---|---|
|Calibration Tool Biped 6dof v1|1|[STL file](stl_files/calibration_tool_biped_6dof_v1.STL)|3d printed part<br>We print this part with the "sparse double dense" setting on our FDM printer.|
|Calibration Tool Biped 6dof v1 - Mirrored version|1|[STL file](stl_files/calibration_tool_biped_6dof_v1_mirror.STL)|3d printed part<br>We print this part with the "sparse double dense" setting on our FDM printer.|
|Calibration Tool Biped 6dof v1 Connector|1|[STL file](stl_files/calibration_tool_biped_6dof_v1_connector.STL)|3d printed part|
|Pin Spacer Tool 4mm|1|[STL file](stl_files/pin_spacer_4mm.STL)|3d printed tool|
|Pin 2mm x 16mm|4|[Online Schrauben](https://online-schrauben.de/shop/Stifte-ohne-Gewinde/DIN-7-Toleranzfeld-m6-Zylinderstifte-Toleranzfeld-m6-aehnl.-ISO-2338-Form-A/Edelstahl-Rostfrei-A1-1.4305/2,0-mm-Durchmesser)|Stainless Steel A1|
|Pin 2,5mm x 12mm|4|[Online Schrauben](https://online-schrauben.de/shop/Stifte-ohne-Gewinde/DIN-7-Toleranzfeld-m6-Zylinderstifte-Toleranzfeld-m6-aehnl.-ISO-2338-Form-A/Edelstahl-Rostfrei-A1-1.4305/2,5-mm-Durchmesser)|Stainless Steel A1|
|Socket Head Cap Screw M3 x 16|4|[Online Schrauben](https://online-schrauben.de/shop/Schrauben/Innensechskantschrauben/ISO-4762-DIN-912-Zylinderkopfschrauben-mit-Innensechskant-aehnl.-DIN-912/Edelstahl-Rostfrei-A2/M-3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)|Stainless Steel A2|
|Threaded Inserts M3 x 4,5|4|[Hoffmann](https://www.hoffmann-group.com/US/en/hus/Power-tools-and-workshop-supplies/Soldering-tools-cleaning-devices-thread-repair/Thread-insert-set%2C-100-pieces-1-5×D/p/082818)<br>[McMaster](https://www.mcmaster.com/91732A647/)|Helicoil|

### Preparing the Calibration Tools
<br>*Calibration tool - pin locations.*<br>

<br>*Use a 1,9mm drill bit to adjust the hole diameters for the 2mm pins.<br>Install the 2mm pins using a hammer.<br>The pins should protrude 4mm from the surface.<br>The [Pin Spacer Tool](stl_files/pin_spacer_4mm.STL) can help to position the pin correctly.*<br>

<br>*Use a 2,4mm drill bit to adjust the hole diameters for the 2,5mm pins.<br>Install the 2,5mm pins using a hammer.<br>*<br>

<br>*Increase the square holes on the side of the connector in small steps.<br>Drill with 2,5mm / 2,7mm / 2,9mm and 3,1mm diameter.<br>Install M3x4,5 Helicoil threaded inserts in all four locations.*<br>

### Installing the Calibration Tools
<br>*Insert the pins into the screw heads of the actuator module and the lower leg.<br>Make sure that the tool is fully seated and that there is no gap between the parts.<br>We use velcro straps around the knees to keep the calibration tools in place.<br>Use M3x16 screws to install the connector part.*<br>

## More Information
[Open Dynamic Robot Initiative - Webpage](https://open-dynamic-robot-initiative.github.io)  
[Open Dynamic Robot Initiative - YouTube Channel](https://www.youtube.com/channel/UCx32JW2oIrax47Gjq8zNI-w)   
[Open Dynamic Robot Initiative - Forum](https://odri.discourse.group/categories)  
[Open Dynamic Robot Initiative - Paper](https://arxiv.org/pdf/1910.00093.pdf)  
[Hardware Overview](../../README.md#open-robot-actuator-hardware)  
[Software Overview](https://github.com/open-dynamic-robot-initiative/open-dynamic-robot-initiative.github.io/wiki)  

---
## Authors
Felix Grimminger

## License
BSD 3-Clause License

## Copyright
Copyright (c) 2019-2021, Max Planck Gesellschaft and New York University

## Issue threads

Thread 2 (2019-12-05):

motorware repo not public yet

jviereck, 2019-12-05:
For flashing the firmware on the TI boards, we rely on the `motorware` repo from git-amd right now. This means anyone outside of amd-clmc won't be able to flash this board.

Is this a problem?

\cc @luator @vincentberenz

luator, 2019-12-06:
We don't have a public fork of motorware due to an unclear legal situation (it is affected by some US export regulation...). However, we provide a patch with our modifications here: https://github.com/open-dynamic-robot-initiative/amd_motorware_ext. So people from outside have to download it from TI first and then can apply this patch.

luator, 2020-02-13:
Closing this as WONTFIX. Feel free to re-open if there is still something to discuss.

Closed 2020-02-13.

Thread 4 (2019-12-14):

motor shaft

f-e-l-i-x, 2019-12-14:
I have a few questions regarding the motor shaft:
- why does the original have to be replaced (is it too short?)
- why does the replacement shaft have a different thickness?
Thanks

thomasfla, 2019-12-14:
Maybe @fgrimminger is the best person to answer, but here is some elements:

Yes, the motor shaft have to be replaced because it is too short. The longer one allows to insert a pulley, an encoder codewheel, and a support bearing. The thickness are the same, it's just that the original tolerances make the fit to tight to be reassembled without special tools, so we adjust the bore diameter with a reamer.

see https://github.com/open-dynamic-robot-initiative/open_robot_actuator_hardware/blob/master/mechanics/actuator_module_v1/details/details_motor_shaft_preparation.md
and
https://github.com/open-dynamic-robot-initiative/open_robot_actuator_hardware/blob/master/mechanics/actuator_module_v1/details/details_motor_preparation.md
for more details;

fgrimminger, 2019-12-16:
The motor is designed for quadcopters - so the propeller is attached to the rotor from the top.
For our design it`s more convenient to extend the output shaft and attach the motor pulley from the opposite side. (see screenshot below) The motor shaft diameter is pretty much the same. For us it's easier to source stainless steel shafts with 3.98mm. That also helps with assembly because the pressfit on the rotor is less tight.
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

Closed 2019-12-16.

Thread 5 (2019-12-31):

center pulley

f-e-l-i-x, 2019-12-31:
Would it be possible to produce the center pulley by wire EDM in a "2D" design, without post-processing in a lathe?

The center pulley would then be cut with a through hole like the motor pulley and a shaft would be inserted into the hole.

Would this suffice for the center pulley to be rotationally supported by its bearings or is a flat surface facing the center pulley bearings unsuitable?

fgrimminger, 2020-01-07:
You could try it....
The problem is that the pulley has a larger diameter than the outer ring of the bearing.
So the pulley could rub on the outer ring or on the shell structure. (see screenshot)
You probably want to add small spacers to prevent that from happening.
Best. Felix
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

Closed 2020-01-07.

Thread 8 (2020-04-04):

AT3 belts?

AlexDaniel, 2020-04-04:
Hi! This project is amazing! Finally, a truly open-source dog-like robot.

I'm just curious, what's the justification for using relatively uncommon AT3 belts (instead of let's say GT2). I'm sure you had a good reason, but what is it?

fgrimminger, 2020-04-06:
Hi - thanks for your interest.
We tested a couple of different timing belts - the main challenge was to prevent tooth skipping under high loads while minimizing friction and backlash.
The Synchroflex AT3 GEN III timing belts consist of polyurethane with steel-cord reinforcements and really tough. Those belts worked well during testing so we settled for them.
The GT2 belts would probably also work fine if you modify the pulley geometry and get the belt tension right.
Best wishes. Felix

Closed 2020-04-06.

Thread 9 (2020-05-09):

Im planning to use this actuator for my 6DOF robotic arm

stejesh, 2020-05-09:
Hi,

Is this a good actuator candidate to be used for a robotic arm with 6 degrees of freedom? Im looking for torque, velocity and a bit of position control (not heavily critical ) what kind of repeatability can I expect from this arm and my approx payload

fgrimminger, 2020-05-11:
Hi,
no - I don't think this is a good candidate for a 6dof arm.
This actuator module was designed for dynamic legged robots.
It's best suited for short high-performance motions and hard impacts.
Handling payloads for longer periods of time will heat up the motors too much.
Also there is no joint sensor on the output - that means the elasticity of the transmission results in end effector position errors. We have not measured the positioning repeatability.
We are using the actuator module for a 3 finger hand: https://github.com/open-dynamic-robot-initiative/open_robot_actuator_hardware/blob/master/mechanics/tri_finger_edu_v1/README.md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
But for a 6dof arm you'll need higher gear ratios or stronger motors for the shoulder actuators.
This would require redesigning a lot of the mechanics.

Closed 2020-05-14.

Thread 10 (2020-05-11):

quadruped_upper_leg

STGRobotics, 2020-05-11:
Thank you for the great work. Where can I find the quadruped_upper_leg base and cover.

Thank you

thomasfla, 2020-05-11:
Hi, Are you talking about the 12dof version?
If yes, the upper leg actuator is the same as the one used for the 8dof.
You can find the files here:

https://github.com/open-dynamic-robot-initiative/open_robot_actuator_hardware/blob/master/mechanics/actuator_module_v1/stl_files/actuator_module_shell_base.STL

and

https://github.com/open-dynamic-robot-initiative/open_robot_actuator_hardware/blob/master/mechanics/actuator_module_v1/stl_files/actuator_module_shell_cover.STL

STGRobotics, 2020-05-11:
Thank you

thomasfla, 2020-05-11:
@fgrimminger Maybe we want to add a link to the files in the .md?

STGRobotics, 2020-05-11:
It would be helpful. The name of the file through me for a loop.

fgrimminger, 2020-05-12:
I agree that it's a bit confusing.
I'll try to restructure the documentation to make it easier to use.
For now I have added the STL files to this folder.
https://github.com/open-dynamic-robot-initiative/open_robot_actuator_hardware/tree/master/mechanics/leg_3dof_v1/stl_files

Closed 2020-05-11.

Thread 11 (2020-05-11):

hip_aa_support/Bearing

STGRobotics, 2020-05-11:
Having problem finding the 20x25x4mm bearing locally. Is it posible to get the step file to modify for a different bearing size.

fgrimminger, 2020-05-12:
Yes - I uploaded the STEP file here:
https://github.com/open-dynamic-robot-initiative/open_robot_actuator_hardware/tree/master/mechanics/quadruped_robot_12dof_v1/step_files
Please note that the wires for the upper leg motor and encoder are routed through this part.
You'll want to make sure that the connectors still fit through the bearing and the support.
Also if you want to maintain the large range of motion the hip aa support  has to clear the upper leg rotor.
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

STGRobotics, 2020-05-12:
Thank you for the file and post. I'm able to find 20x27x4mm bearing easily.

STGRobotics, 2020-05-12:
Found plastic bearing very affordable, to reduce the weight of the robot.

https://www.igus.com/product/460
B6704B3G 20x27x4mm  2.62 USD
B6705B3G 25x32x4mm  2.62 USD

fgrimminger, 2020-05-12:
Thanks - this is interesting....

Closed 2020-05-14.

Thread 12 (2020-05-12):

Printer tolerance

STGRobotics, 2020-05-12:
Unable to print on school 3D printer until school reopen, I have a printer that the tolerance are different. I need to modify the following. Is it posible to get the step file. I was able to mod the body

Actuator Module Shell Base
Actuator Module Shell Cover
Lower Leg Structure Base
Lower Leg Structure Fork
hip_aa_module_shell_base
hip_aa_module_shell_cover
hip_fe_module_shell_base
hip_fe_module_shell_cover
upper_leg_shell_base
upper_leg_shell_cover

fgrimminger, 2020-05-13:
Sure - I uploaded the step files:
https://github.com/open-dynamic-robot-initiative/open_robot_actuator_hardware/tree/master/mechanics/foot_contact_switch_v1/step_files
https://github.com/open-dynamic-robot-initiative/open_robot_actuator_hardware/tree/master/mechanics/quadruped_robot_12dof_v1/step_files

You won't need the actuator module - this version is only used for the Solo8 robot.
It's really the same part as the upper leg - except there are two attachment points and an opening for the wires. This is required, because the same module is used as an upper leg and a hip module for Solo8 (picture below).
I'll restructure and rename the files to make things clearer when I have time.

https://github.com/open-dynamic-robot-initiative/open_robot_actuator_hardware/tree/master/mechanics/actuator_module_v1/step_files

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

STGRobotics, 2020-05-13:
Thank you

Closed 2020-05-14.

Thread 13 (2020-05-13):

Hex Drive Flat Head Screws

STGRobotics, 2020-05-13:
I counter sink the body_structure_center, body_structure_side. Provides a larger grip surface area. Below are the flat heads I'm using. Would like the step file.

M2.5
https://www.mcmaster.com/91294a022-91294A022

M3
https://www.mcmaster.com/91294a134-91294A134

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

fgrimminger, 2020-05-14:
You can find the step files here now...
https://github.com/open-dynamic-robot-initiative/open_robot_actuator_hardware/tree/master/mechanics/quadruped_robot_12dof_v1/step_files

STGRobotics, 2020-05-14:
I meet to say, I modified the files and would you like to have them. Regardless thank you for uploading the step files.

STGRobotics, 2020-05-17:
Replacing metal screw with nylon slotted flat head screws to make bot lighter. Below link is where I purchased from.

https://www.mcmaster.com/plastic-screws/material~plastic/material~nylon-plastic/head-type~flat/thread-type~metric/length~16millimeters/

fgrimminger, 2020-05-18:
o.k. - thanks - please let us know if this modification works well for you.

Closed 2020-09-02.

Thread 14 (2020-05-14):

Custom Electronic Boards

STGRobotics, 2020-05-14:
Looking at replacing the Custom Electronic Boards with Optical Sensor

https://www.mouser.com/ProductDetail/Optek-TT-Electronics/OPB616?qs=a8pkJuPGWJ85yUPzFvMcew%3D%3D

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

thomasfla, 2020-05-14:
Hi,
It could be a good idea! Unfortunately you will make a 1d sensor instead of 2d (lateral forces will not be perceived).
Also you will need some resistors to polarize the transistor and current limit the LED, so in the end it could be also quite complicate. I'm not sure about the weight of the OPB616 sensor, at the location, it is critical!
This foot sensor was design for solo8, but we are not sure about solo12 since the force really is 3d now.. We are trying to develop controller that do not need to contact sensor and estimator that can tell us if the foot is in contact.

STGRobotics, 2020-05-14:
Your correct did not take into consideration 2/3d, thank you.

STGRobotics, 2020-05-14:
How about using force sensing resistors (FSR) and IMU.

fgrimminger, 2020-05-18:
That should also be possible.
At the moment on each motor driver board there are two analog input channels available that are transmitted at 1kHz. One of them is used to measure the foot contact sensor signal. You can connect any other sensor with 0V-3.3V range.
Integrating the imu communication into the micro-controller would probably take quite a bit of effort.

Closed 2020-09-02.

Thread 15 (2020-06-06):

Dual Motor Testbed STL

fcaponetto, 2020-06-06:
Hi,

First, I would say thanks for all the effort that you put on this project. Especially, the well documented steps for the open source community!

I noticed that the "Dual Motor TestBed" project STL file is missing. Therefore, I would like to kindly ask you whether you can also share that project:

https://github.com/open-dynamic-robot-initiative/open_robot_actuator_hardware/raw/master/mechanics/dual_motor_testbed_v1/images/dual_motor_testbed_2.jpg

Thank you in advance.

fgrimminger, 2020-06-08:
Hi,
thanks for your interest.
You can find all the required STL files here now: https://github.com/open-dynamic-robot-initiative/open_robot_actuator_hardware/blob/master/mechanics/dual_motor_testbed_v1/README.md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

I also added an eDrawing assembly file that might be useful:
https://github.com/open-dynamic-robot-initiative/open_robot_actuator_hardware/blob/master/mechanics/dual_motor_testbed_v1/README.md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

Best wishes.

fcaponetto, 2020-06-10:
Thanks a lot!

Closed 2020-09-02.

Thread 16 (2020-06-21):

Machined parts

njdjacobs, 2020-06-21:
The show-stopper for me is the requirement for machined parts. Not everyone has access to the necessary equipment to make these (or the skills to use it).

Can anyone suggest how to source these parts (preferably in Europe)?

fgrimminger, 2020-06-23:
You'll want to search for machine shops in your region and ask for quotes.
The machining of the pulleys becomes easier if you provide a custom form cutter for the tooth geometry. For that you'll first have to find a tool manufacturer that can produce the custom form cutter: https://github.com/open-dynamic-robot-initiative/open_robot_actuator_hardware/blob/master/mechanics/actuator_module_v1/details/details_machined_parts.md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

Alternatively you could request a quote from an online manufacturing service.
We haven't tried this yet so we have no experience regarding the quality and cost - but we'll be looking into this topic soon.
Here are some companies that we found:
https://www.rapiddirect.com/
https://www.facturee.de/en/about-us/

njdjacobs, 2020-06-23:
Thanks for the advice and links.

Closed 2020-09-02.

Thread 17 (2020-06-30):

Costs, sources

i-make-robots, 2020-06-30:
Hi!  Love the project.  Very interested in the encoders.

How much did they cost you?  An approximate idea of the build cost for the entire bot would be nice to have, and these encoders are of particular interest to me.

How did you find them in the first place?  I'm always looking for better sources.  Since your search-fu outdoes mine, I wish to learn your technique.

Thank you!

fgrimminger, 2020-07-06:
Hi! Thank you.
Yes - the encoders are nice - high resolution and very reliable.
I first saw the encoder being sold with Maxon and Faulhaber motors many years ago.
You can find the encoder kit using this product number: AEDM-5810-Z12
DigiKey and Mouser sell them for around 45€/piece.
Here is a short description on how to disassemble the kit:
https://github.com/open-dynamic-robot-initiative/open_robot_actuator_hardware/blob/master/mechanics/actuator_module_v1/details/details_encoder_kit_disassembly.md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

The material cost for the Solo 8 robot is around 4000€  - for the Solo 12 robot around 6000€.

Here is another interesting encoder - it has the highest resolution that I could find for this size (80.000cpr!) but more complex electronics.  http://www.downloads-numerikjena.de/sheets/UM_ULTHEMIUS_eng.pdf

i-make-robots, 2020-07-06:
Nice!  And just to confirm... these are not absolute encoders, right?

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

fgrimminger, 2020-07-06:
Right - the Broadcom and the Ulthemius encoders are incremental encoders with an index pulse (ABZ).

Closed 2020-09-02.

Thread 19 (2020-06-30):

reference error, biped leg -> 3dof leg, not 3dof biped leg

maidenone, 2020-06-30:
on page:
https://github.com/open-dynamic-robot-initiative/open_robot_actuator_hardware/blob/master/mechanics/biped_6dof_v1/README.md

section:

Part Name | Quantity | Ordering Information | Comments
-- | -- | -- | --
Biped Leg 3DOF Right Side | 1 | Biped Leg 3DOF Documentation | Custom assembly
Biped Leg 3DOF Left Side | 1 | Biped Leg 3DOF Documentation | Custom assembly

links leads to:
https://github.com/open-dynamic-robot-initiative/open_robot_actuator_hardware/blob/master/mechanics/leg_3dof_v1/README.md

but it should go to:

https://github.com/open-dynamic-robot-initiative/open_robot_actuator_hardware/tree/master/mechanics/biped_leg_3dof_v1

fgrimminger, 2020-07-06:
Thank you for reporting this. I fixed the links.
Please let us know if you find any other errors.

Closed 2020-07-06.

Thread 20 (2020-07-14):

firmware

1027743011, 2020-07-14:
Hi!
    Thank you for share this magic project.I love this project and i want  to make  a  quadruped robot 8dof v1  by myself.
    I  noticed the firmware  in the "open-motor-driver-initiative"   was temporarily hosted in this private repository: https://gitlab.laas.fr/open-dynamic-robot-initiative/omodri.  And  I can't connect to this website.This question has puzzled me for a long time.Therefore, I would like to kindly ask you whether you can also share that project.Thank you very much!

fgrimminger, 2020-07-15:
Hi,
thanks for your interest.

You can find instructions on how to download and patch the firmware here:
https://github.com/open-dynamic-robot-initiative/amd_motorware_ext#amd-motorware-extensions

The firmware is based on the Texas Instruments Motorware library.
We cannot make the modified firmware available, because TI requires you to confirm that you won't violate their export regulations before downloading Motorware.

1027743011, 2020-07-23:
HI,
thanks for your reply.I have successfully downloaded  MotorWare v1.01.00.18 from the TI website.But I can’t log in to the website where the source code is saved.Can this source code be published？I am a graduate student and I find it difficult to understand all the codes.So I want to ask if the source code will be published in other ways.
Thank you very much anyway!

jviereck, 2020-07-24:
Hi @1027743011 ,

I assume you are using the TI launchpads with CAN communication for your project? If so, the source code is open source.

What you need to do is clone the following repos in the same folder:

- https://github.com/open-dynamic-robot-initiative/mw_dual_motor_torque_ctrl
- https://github.com/open-dynamic-robot-initiative/user_config_f28069m_drv8305
- https://github.com/open-dynamic-robot-initiative/amd_motorware_ext

This looks then like this:

```
workspace
├── amd_motorware_ext
├── mw_dual_motor_torque_ctrl
└── user_config_f28069m_drv8305
```

Then follow the [instructions](https://github.com/open-dynamic-robot-initiative/amd_motorware_ext) in the `amd_motorware_ext` to prepare the `motorware` folder.

Finally, you need to flash the TI board. For this, you can follow the documentation from the udriver boards. See the instructions [here](https://github.com/open-dynamic-robot-initiative/udriver_firmware/tree/master/firmware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).

Let me know if you have any questions left.

Best,
Julian

Closed 2020-09-02.

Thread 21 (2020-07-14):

Will the project be providing more detailed BOMs for some of the various mechanical configurations?

androiddrew, 2020-07-14:
Will the project be providing more detailed bill of materials for some of the various mechanical configurations? A huge challenge for me getting started with experimenting with a new design is sourcing all the materials. Some projects I have followed have provided a BOM for a standard configuration(with suppliers) which had me up and running in under a month.

Even if this isn't added to the project page, could one of the maintainers be encouraged to provide maybe a blog post(or several) on a build?

easybuildtech, 2020-07-14:
I have been trying to source the machined parts.  Perhaps we can get a
handful of folks interested to commit in order to spread the setup costs
out?  The rest of the components I have been able to source relatively
effectively.

---
Benjamin R Smith
0bensmith0@gmail.com
c: 248 941 4022

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

fgrimminger, 2020-07-16:
Yes - we'll work on adding detailed bills of materials next.

Teaming up for ordering machined parts is a good idea.

We have setup a Discourse forum for questions and collaboration.
[https://odri.discourse.group/categories](url)

fgrimminger, 2020-07-20:
The bill of materials for the core components of the actuator module  can be found here now:
https://github.com/open-dynamic-robot-initiative/open_robot_actuator_hardware/blob/master/mechanics/actuator_module_v1/README.md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

wujiang, 2020-11-20:
@easybuildtech did you manage to get those mechanical parts?

MusubaPy, 2021-02-09:
Your project is _amazing_!

Can I use TMS320-XDS100-V3, JTAG instead of Spectrum Digital XDS100V2 JTAG?

Please advise what can be used instead of Lord Microstrain 3DM-CX5-25?

fgrimminger, 2021-02-10:
Thank you!
The TMS320-XDS100-V3 programmer should work but we haven't tested it.
I don't know about IMU alternatives - the master board electrical interface and firmware was designed for the Microstrain IMU.
If you want to use a different IMU you'll have to adapt the firmware and possibly the the electrical interface.
Alternatively you could use an external motion capture system for base estimation - that's what we've been using for a lot of the experiments in the past.
We also have a [Forum](https://odri.discourse.group/latest) now where you can ask questions and discuss alternative components.

wangyear, 2023-07-16:
Hi, my friends, I'm sorry to bother you to tell me that what the sensors have you used in your projects, and its concrete information.
Thank you very much, I'm looking forward to your reply.

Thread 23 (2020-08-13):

Identification of Torque-Current constant k_i

juanmed, 2020-08-13:
Hi

Thank you for sharing such an awesome robotics initiative.

According to your [paper in arxiv](https://arxiv.org/abs/1910.00093), the constant k_i relates the joint torque and the current of the motor. Since this parameter is a property of the motor, could you please comment on the experimental procedure to measure it?

Thanks!

fgrimminger, 2020-08-17:
Hi,
we applied different currents to the motor and measured the output torque using a pulley, a string and a digital force meter.

Another option is to measure the velocity constant of the motor and calculate the torque constant from that.
Here is a good explanation: https://things-in-motion.blogspot.com/2018/12/how-to-estimate-torque-of-bldc-pmsm.html

juanmed, 2020-08-17:
Thanks for your reply.

Closed 2020-08-17.

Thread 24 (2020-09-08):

Gerber files for contact switch

Sreevis, 2020-09-08:
Hi, Thanks for this wonderful contribution.

I wish to make the 12 DOF robot configuration.
I noticed a few things while checking the [foot contact switch PCB](https://github.com/open-dynamic-robot-initiative/open_robot_actuator_hardware/blob/master/mechanics/foot_contact_switch_v1/documentation/foot_contact_switch_v1.zip))

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

The .brd file doesn't have copper pouring as shown in the Picture, sensor out track is broken, r6 is shorted .   and Wire strap pins which I supposed to be external to the PCB is in the .Brd file.

Do you have the Gerber files for the foot contact switch?

fgrimminger, 2020-09-15:
Thanks for your feedback.
You are right - we must have uploaded the wrong version.
We are looking into it.

fgrimminger, 2020-09-30:
Hi,

Joshi Walzog has corrected the Eagle files and has provided the Gerber files for the foot contact switch.

You can find the files here now:
(https://github.com/open-dynamic-robot-initiative/open_robot_actuator_hardware/blob/master/mechanics/foot_contact_switch_v1/README.md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)

Sreevis, 2020-10-01:
Thank you Felix and Joshi. :+1:

Closed 2020-10-01.

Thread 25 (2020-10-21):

Motor selection

juanmed, 2020-10-21:
Hi,

Thanks again for sharing this awesome project and design files. If possible, I would like to ask a rather general question: what was the design criteria to select the T- Motor Antigravity 4004, 300KV motor for the robot? The paper talks briefly on its torque characteristics and that, in general, weight is a major factor. Narrowing down, I would like to know more on your selection process, if there were any soft/hard requirements you wanted to satisfy, if you tested other motors, and any other considerations you had.

Thanks for your time!

fgrimminger, 2020-10-22:
Hi,
thanks for your interest.

For this project we were looking for a high torque and low rotor inertia motor with a weight of around 50g.
Brushless outrunner motors with a high number of pole pairs and a low KV value are best suited.
We estimated that a torque constant of 0,02Nm/A would be required for high performance behaviors with a low gear ratio transmission of around 10:1 and motor drivers that can deliver up to 15A.
We looked at some hobby rc and quadcopter motors but didn't do much performance  testing.

Most motors we looked at were too heavy, too tall for our design or the KV value was too high.
We were interested in a motor with minimal height because that influences how much the leg segments need to be offset in this arrangement. (screenshot below)
The Antigravity motors have the perfect form factor, a torque constant of around 0,02Nm/A, are very high quality and can be modified easily to fit our design.
As a research lab that can only order components on invoice it was also important that the motor would be available for many years from resellers in Germany that would deliver on invoice.

At the time (2016) there were not so many choices available - today there might be better options.
Ben Katz has posted a comparison of different motors that he has tested:
[Motor Characterization](http://build-its-inprogress.blogspot.com/2016/01/motor-characterization-for-small.html)

Please let us know if you find a motor that you consider superior.
You can also use the[ forum](https://odri.discourse.group/categories) to discuss questions like this with us and others.

Best. Felix
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

juanmed, 2020-10-22:
Hi, thank you for the detailed answer and taking the time for the screenshot, this is very informative. Indeed, I am looking for other motors. Thanks for pointing out the discussion forum, I will for sure use it and let you know if I find anything worth considering.

fgrimminger, 2020-10-22:
Hi,
you are welcome.
Good luck and best wishes,
Felix

Closed 2020-10-22.

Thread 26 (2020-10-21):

Motor stand pose angles

nicrusso7, 2020-10-21:
Hi there,
this project is awesome!
I'm trying to simulate the 12DOF model and I was looking for the default motor angles when the robot stands.
Thanks!

jviereck, 2020-10-21:
Hi,

they are defined here: https://github.com/open-dynamic-robot-initiative/robot_properties_solo/blob/master/python/robot_properties_solo/config.py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

Closing the issue. Feel free to open it again.

Best,
Julian

Closed 2020-10-21.

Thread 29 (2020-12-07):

Connecting The Finger Optoswitch Connector

HanTop310, 2020-12-07:
Hi there, I need your help in proving me an idiot.
Can you please show me on the MASTER-BOARD where is the Finger Connector is connected?
Is it connected on the MICRO-DRIVER? Where?

fgrimminger, 2020-12-07:
Hi,
we connect the optical sensor to one of the analog-in ports of the micro driver board.
There are two analog-in ports available per board (ADC-A6 and ADC-B6).
Both analog measurements are transmitted through the masterboard to the control pc at 1kHz.
The pins are marked in the screenshot below - you could use a 3 pin connector for connecting one optical sensor or a 4 pin connector for connecting two optical sensors.
Make sure to use the 3.3V supply voltage - the analog inputs don't tolerate higher voltages.
Best. Felix
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

HanTop310, 2020-12-07:
Does it matter to which micro driver i connect? cause there are 6 micro drivers (in the 12dof) and 4 sensors

fgrimminger, 2020-12-08:
No -  it doesn't matter - you will just need to process the right sensor values from the data stream.
You can connect the optical sensors to any micro diver board.
All 12 analog-in channels are transmitted to the pc.
I would connect one sensor to each of the top two cards in the front and in the back.
That way you have separate 3pin connectors for each sensor - and the upper cards are easier to access.
We use the [90 degree Hirose connectors ](https://github.com/open-dynamic-robot-initiative/open_robot_actuator_hardware/blob/master/electronics/details/details_components.md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) on the micro driver board - that makes it easier to plug and unplug the sensors on the robot.

Closed 2021-01-11.

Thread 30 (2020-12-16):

Motor and sensor replacement questions for my practical local setup.

taskx6004, 2020-12-16:
Hi, I want to build a drive unit to test functionalities before building 12 units of them, with some modifications with motor and sensor, here's something would you please give me some hint:

1. 300KV 4004 from TMotor is way to expensive as a RC motor, I want to replace it with DJI Inspire 1/2 generation 3510H, same KV but smaller diameter. It has a shaft could be used as a pinon guide, and four quirky vertical tab for screw mounting. I think i can redesign the belt transmission so this is not an issue, it's for forking suggestion for people who want's build their own like me.

2. encoder: In the documenting [https://github.com/open-dynamic-robot-initiative/open_robot_actuator_hardware/blob/master/mechanics/dual_motor_testbed_v1/README.md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](here) claimed it has a 5000 pulses! AB encoding with times 4 on it so the resolution is 20000 per turn. it almost impractical in my sense for a motor like this. By taking this concern I looked for its datasheet: **CPR=625 and res = 5000**. An AS5047 magnetic encoder with 1000 CPR would worth a compatibility/performance test. And one more favorable feature is much easier to mount the small surface polarized tablet for sensing.

3. How to acquire TI instaspin related code, modify the ABI settings. etc. would a stock firmware could work with ORAH software?

Thanks for the effort for the project.

fgrimminger, 2020-12-20:
Hi,

starting with building and testing one actuator module is a good approach.

1. The Antigravity 4004 motors are sold in sets of two pieces - the price per piece is around 60€.
You could use a cheaper motor if you modify the mounting interface and the motor shaft.
The ESC motor driver electronics that they sell with the motor are used for quad-copters but are not suitable for torque-control of a legged robot.

2. That's right - the encoder discs we use have 625 lines - the encoder produces 5000 pulses per turn and channel from that.
On the motor driver boards we use the rising and falling edges from the A and B channels and get 20.000 counts per revolution.
The reason why the high resolution is important for us is because the velocity is calculated from the position measurement.
For high performance control we need a velocity signal that's as smooth and precise as possible.
For that we calculate and filter the velocity signal at 10kHz on the motor driver boards - and we would like to have the highest angular resolution possible.

3. I don't understand this question.

You can also use the [Forum](https://odri.discourse.group/latest) to discuss your questions and ideas for improvements.

Best wishes. Felix

Closed 2021-01-11.

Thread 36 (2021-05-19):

Cable routing improvement proposal solo12

pamartinez-pal, 2021-05-19:
We are building a solo 12 in pal-robotics and we have found the cable routing around the shoulder joint very complicated. We had some issue with the cables being torn by the consecutive 90º forlds.

The assembly would be much simpler and durable if the cable channel was 3 to 5 mm wider. Would it be possible to expand the "Body Structure Hip AA Support" such that it has more room for the cabling.

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

Thank you.

fgrimminger, 2021-05-20:
True - the internal wire passage is pretty tight.
I increased it by 3mm - from 4mm to 7mm.

You can find the updated STL file [here](https://github.com/open-dynamic-robot-initiative/open_robot_actuator_hardware/blob/master/mechanics/quadruped_robot_12dof_v1/stl_files/body_structure_hip_aa_support_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).
Does this solve your issue?

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

Best. Felix

pamartinez-pal, 2021-05-20:
Great!

Thank you.

Closed 2021-05-20.

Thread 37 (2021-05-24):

Untethered version, Support additional mass of battery pack

bcbuckles, 2021-05-24:
First off, great work! This is a great contribution to open source robotics community, very exciting.  I am curious if anyone has attempted an untethered version, or done an analysis of the loads, joints, actuator sizing, etc to see if its even feasible.  I understand the control scheme and electronics are currently designed for tethered operation, but I'm curious whether the hardware /actuators could be extended to an untethered build without much modification.  Of course the torque/mass relationship is of utmost importance in these types of robots, and i expect that your actuators were sized for the current mass.  Anyhow, I would love to build an untethered version with a custom li-ion or lipo pack, but was hoping you could share some insight or any calc/research you've done on the subject.

bcbuckles, 2021-05-26:
It appears v1.1 is looking into this. Closing

Closed 2021-05-26.

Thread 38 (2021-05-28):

Cable Routing improving proposal

nitrostormbcn, 2021-05-28:
Hi, I'm Pau from PAL Robotics, we have found some improvement in the part "hip_fe_module_shell" that would greatly improve cable routing. We've had problems assembling the shoulder and this would ease manufacturing without changing the robot's geometry.

Before:
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

After:
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

It only modifies the external shell and help routing. I can send you the modified part if you wish.
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

fgrimminger, 2021-05-28:
Hello Pau,

thanks for your suggestions.

I am surprised to hear that you have so much trouble with the wire routing through the hip.
Are you using the same encoder and motor phase connectors that we are using? ([Details Wiring](https://github.com/open-dynamic-robot-initiative/open_robot_actuator_hardware/blob/master/electronics/details/details_wiring.md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))

What kind of wires are you using?
We had bad experiences with ribbon wires.

I first pull the encoder connector and wires through - then the three motor phase wires - one after the other.
Using pliers helps sometimes.

Best. Felix

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

nitrostormbcn, 2021-05-31:
We've had problems with the cables getting twisted over each other and stripping the insulation, this should be alleviated with looser cable routing.

Also when replacing the broken wires, disassembly and reassembly was very tedious.

Imho, I think this problems would be solved by allowing more space for the cables to pass.

fgrimminger, 2021-08-23:
Hi Pau,

o.k. - thanks for your suggestion and the stl file.
I added it to the [3dof leg documentation](https://github.com/open-dynamic-robot-initiative/open_robot_actuator_hardware/tree/master/mechanics/leg_3dof_v1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).

Best,
Felix

dvogureckiy99, 2022-10-26:
good afternoon, thanks for the improvement, could you please provide a model in the extension .step or .SLDPRT, not .STL because all sizes are losted in it.

Closed 2021-08-23.

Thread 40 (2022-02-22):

Wrong resistors values

jochenalt, 2022-02-22:
Hi all, the schematics of the foot sensor uses a voltage divider via R4/R5, which gives a reference voltage of 2.2V, which is too high for the photosensor used. As a result, the opamp never indicates an illuminated sensor. The voltage divider should rather be something around R4=51K R5=5.1K resulting in a voltage of 0.3V.
Cheers,
Jochen

fgrimminger, 2022-02-23:
Hello Jochen,

o.k. - I'm glad to hear that it's working for you.

Good idea - thanks for sharing your modifications.

Best,
Felix

Closed 2022-03-07.

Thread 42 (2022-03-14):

what is the recommended power supply？

FranCOOlin, 2022-03-14:
I decide to use a switching power supply, but how much current it may consume during normal operation at the voltage of 24V ?

fgrimminger, 2022-03-21:
We use a 30A power supply - you can find more information here:
https://github.com/open-dynamic-robot-initiative/open_robot_actuator_hardware/blob/master/electronics/details/details_components.md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

The current draw will depend on the gait of the robot - on average it's typically around 3-5A.
The problem with the power supplies isn't so much the maximum rated current but the lack of dynamic response.

For a jumping behavior for example all the motors will draw a high current at the same instance.
That can cause the voltage to drop if the power supply isn't dynamic enough to supply that current peak.

If the voltage at the motor drivers drops below 8V the microcontrollers on the motor driver cards will reset.
So for the high jumps we were using two power supplies - one to power the front legs and one to power the hind legs.
https://www.youtube.com/watch?v=javHeKRKbAc

FranCOOlin, 2022-05-01:
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

Thank you. Now I've got basic ideas about it.

Closed 2022-05-02.

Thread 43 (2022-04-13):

Missing SOLIDWORKS Parts of quadruped_12dof_v1.1

acromtech, 2022-04-13:
Do you have SOLIDWORKS Parts of the quadruped_12dof_v1.1 ?
I need it because I currently work on the Solo head and I only find STL files.
Thanks.

fgrimminger, 2022-04-13:
Yes - you can find the Solidworks files here now:
https://github.com/open-dynamic-robot-initiative/open_robot_actuator_hardware/tree/master/mechanics/quadruped_robot_12dof_v1.1/solidworks_files

Best. Felix

Closed 2022-05-02.

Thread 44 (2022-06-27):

3D Print STL File Link/Location for the actuator model base and cover

autonomousTurtle, 2022-06-27:
Currently, the actuaor base and cover STL files are not inluded in the list of [STL files](https://github.com/open-dynamic-robot-initiative/open_robot_actuator_hardware/tree/master/mechanics/actuator_module_v1/stl_files) A search on the repo points to a folder in the [leg_2dof_v1](https://github.com/open-dynamic-robot-initiative/open_robot_actuator_hardware/blob/master/mechanics/leg_2dof_v1/stl_files/actuator_module_shell_base_outdated.STL) where the file has 'outdated' in the name. Is this still the shell to use or is there a more recent file? Thank you!

autonomousTurtle, 2022-06-27:
Ah this helped point me in the right direction, thank you!

I am building the trifinger EDU, and found [this](https://github.com/open-dynamic-robot-initiative/open_robot_actuator_hardware/blob/master/mechanics/finger_edu_v1/README.md) based off of what you sent back!

Thanks!

Closed 2022-06-27.

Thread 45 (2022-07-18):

Foot Contact Switch connection

dvogureckiy99, 2022-07-18:
Hi, how does Foot Contact Switch v1 connect to Micro Driver ?
As I understand it connects to ADC to one of the Micro Driver MCU via U$12 contact.

fgrimminger, 2022-07-19:
Hi,
each Micro Driver has 2 ADC ports which are evaluated and transmitted at 1kHz.
You want to supply the foot sensor with 3.3V - that's the maximum voltage of the ADCs.
In this schematic the ADC ports are labeled with ADC-A6 and ADC-B6.
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

dvogureckiy99, 2022-07-19:
that is, I can connect 2 sensors to one board udriver?

fgrimminger, 2022-07-19:
Yes - that's possible.
In that case the sensors will have to share the 3.3V and GND connection.
It might be less convenient for assembly and repairs to have both sensors on a single Hirose connector.
It might make sense to connect one sensor per Micro Driver board and use a individual 3pin Hirose connector for each one.

dvogureckiy99, 2022-07-19:
Thanks!

fgrimminger, 2022-07-19:
Welcome!

Closed 2022-07-19.

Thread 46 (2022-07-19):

How can I calibrate the Quadruped 12dof (Solo12) ?

dvogureckiy99, 2022-07-19:
How can I calibrate the Quadruped 12dof (Solo12) ?

fgrimminger, 2022-07-19:
We use a calibration tool to find the zero position of the legs.
Do you have that tool?
https://github.com/open-dynamic-robot-initiative/open_robot_actuator_hardware/blob/master/mechanics/general/robot_calibration.md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

Closed 2022-08-03.

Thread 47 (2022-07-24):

Part weight

MEE2022, 2022-07-24:
Do you have any instructions or advice for how to get the correct part weights for 3D resin printing without wasting a ton of time and resin?    How far off can the part weight be (this isn't a very well posed question because it's too general) without the inertia measurement unit and the software failing to perform correctly?

Thank you in advance and thank you for this project.

fgrimminger, 2022-07-26:
Hi,
don't worry about matching the exact weight of the 3d printed parts in the assembly.
Minor differences in the part weight will have only minimal effect on the inertia and the behavior of the robot.
What's more important are the material properties and the tolerances of the parts.
For the structural parts like the shells we recommend to use a FDM printer like a Fortus or a Ultimaker printer.
The parts from FDM printers are usually cheaper, have shorter print times and and higher impact resistance compared to SLA parts.
For the pulleys the tolerances of the teeth are critical - for those parts we recommend to use a SLA or Multijet printer like a Projet or Formlabs printer.

Here is some more information: https://github.com/open-dynamic-robot-initiative/open_robot_actuator_hardware/blob/master/mechanics/actuator_module_v1/details/details_3d_printed_parts.md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

Best wishes. Felix

Closed 2022-08-03.

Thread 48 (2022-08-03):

Minimum tensile strength

MEE2022, 2022-08-03:
I understand you recommend the lower legs be manufactured using carbon fiber, but do you have some minimum strength parameters on this part?  I was wondering if I might be able to resin print it using Liqcreate Strong-X ([technical resin data sheet](https://www.liqcreate.com/product/strong-x/#technical))

I know the tensile strength between carbon fiber and this resin are orders of magnitude off.  I haven't done a proper in-depth project overview to get a precise understanding of the stresses on this part.  Please excuse me if this is a stupid question.

fgrimminger, 2022-08-03:
Hi,
that's a valid question - it's not so easy to select the right material and printing technology for the different parts.
So far we've been mostly using lower legs that were printed on an FDM printer with [PC-ABS material](https://www.stratasys.com/contentassets/0cbbbe43e9ab4200a16c507eb99ebe7e/mds_fdm_pc-abs_0222a2.pdf?v=49c744).
For the quadrupeds we're using the [lower leg v2](https://github.com/open-dynamic-robot-initiative/open_robot_actuator_hardware/blob/master/mechanics/general/lower_legs.md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) with sparse infill to reduce the weight.
We haven't broken any lower legs yet - so the tensile strength has not been an issue.
What seems more problematic is that the low lateral stiffness of the lower legs that can lead to vibrations depending on the gait and the gain and damping settings of the controller.
That's why we have reinforced the biped lower legs with [carbon fiber layer](https://github.com/open-dynamic-robot-initiative/open_robot_actuator_hardware/blob/master/mechanics/biped_leg_3dof_v1/README.md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). We have also used lower legs from an Markforged printer that has the capability to embed continuous fibers inside of the part.

To answer your question:
I would recommend to start printing the lower legs v2 on an FDM printer with sparse infill.
You could also try to print lower legs on your resin printer - the v2 version will be pretty heavy, because I don't think that you can print sparse structures inside of the part. So you could use the [v3 lower leg version](https://github.com/open-dynamic-robot-initiative/open_robot_actuator_hardware/blob/master/mechanics/general/lower_legs.md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) that is made for solid printing.  You could print the lower legs with both materials and see what works best for you.

 I'd be mostly concerned about the low impact resistance of the photopolymer materials - our experience is that those materials are rather brittle and break or crack easily under impact loading. You can also see that in the datasheet  - the IZOD Impact value is only 20 J/m. For the FDM material it's around 240 J/m with the printing orientation that we  use.

Closed 2022-08-15.

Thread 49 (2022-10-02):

details_actuator_module_testing.md is still empty,how can I test the module before all stacked together?

vxgu86, 2022-10-02:
like what I asked in the title, how can I test the module before all stacked together?

https://github.com/open-dynamic-robot-initiative/open_robot_actuator_hardware/blob/master/mechanics/actuator_module_v1/details/details_actuator_module_testing.md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

by the way, it's really nice job.

thomasfla, 2022-10-03:
Hi, you can connect the module to the masterboard and the masterboard to a PC and run this example: https://github.com/open-dynamic-robot-initiative/master-board/blob/master/sdk/master_board_sdk/example/example.py

It should move the motor following a sinusoidal motion and display all the data from the actuator (position, velocity, current, index detection etc..)

vxgu86, 2022-10-03:
thanks, I also want to ask another small question, it's about the code wheel in [this link](https://github.com/open-dynamic-robot-initiative/open_robot_actuator_hardware/blob/master/mechanics/actuator_module_v1/details/details_encoder_kit_disassembly.md)

*The aluminum collar on the code wheel has to be removed on a lathe.
Cover the optical disc with tape to protect from scratching.*
what do you mean by "removed on a lathe", should the aluminum collar be cutted off, or grind off?
and by the way, how to clamp the codewheel with your tool in [this link](https://github.com/open-dynamic-robot-initiative/open_robot_actuator_hardware/blob/master/mechanics/actuator_module_v1/details/details_encoder.md)?

fgrimminger, 2022-10-05:
We use a "parting-off tool" to cut off the collar on a lathe - there's a picture below.

We clamp the code wheel on the smaller diameter of the tool using a M3 screw and washers.

The larger diameter of the tool is held by the chuck of the lathe.

Alternatively you can order the motor shaft assembly with code wheel from PWB - as described [here](https://github.com/open-dynamic-robot-initiative/open_robot_actuator_hardware/blob/master/mechanics/actuator_module_v1/actuator_module_v1.1.md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).

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

vxgu86, 2022-10-17:
@fgrimminger thanks for your reply.
I tried one,but get the wheel twisted， not flat as original, not tested yet, don't know whether it would affect the performance.
by the way I did get the meaning of the first pic.

fgrimminger, 2022-10-18:
Hi,
o.k. - it might still work if it's not twisted too badly.
The encoders are pretty robust to misalignment and inaccuracies.
Just make sure that the code wheel doesn't touch the encoder when it's spinning - otherwise the disc will get scratched.
The motor control firmware checks how many pulses have passed every time the index pulse is recognized.
If the discrepancy is more than a couple of ticks the card will stop and report an encoder error.

Do you mean you **didn't** get the meaning of the first picture?
The first picture shows a parting-off tool - similar to what we use to remove the aluminum flange on a lathe.
If you do a web search for "parting-off tool" you'll find more variants and information.

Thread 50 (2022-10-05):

Q: what's the total estimated cost of the hardware?

mw66, 2022-10-05:
Just want to get a rough idea.

Thanks.

fgrimminger, 2022-10-11:
The price of the robot is difficult to estimate precisely since it will depend on the suppliers and machine shops that you use, the country you are in and the part quantities that you are ordering.

We have estimated the material cost for our Solo12 robot at around 6300€ + tax.
That is not including the imu which is the most expensive part on the robot.

PAL Robotics offers a kit with all the parts and alternatively a preassembled robot.
You can request a quote here: https://solo.pal-robotics.com/solo

easybuildtech, 2022-10-14:
Hi Pascal, check out https://odri.discourse.group/categories for a discussion forum.

fpgirard, 2022-10-14:
@easybuildtech - this is perfect - thank you.   I'm a huge fan of the University of Maryland where many of my interns matriculate.   Some of them are at JPL now (Nick R and Camden S.).    I'm liking what UMCP is posting [here](https://odri.discourse.group/t/interested-in-making-a-modified-less-expensive-solo12/140) - it's consistent with my initial observations.

thomasfla, 2022-10-15:
Hi, thanks for your interest!
indeed the [forum](https://odri.discourse.group/) is the good place to discuss such topic.

I can start here with a few element of answer.
Despite being mostly 3d printed, solo and other ODRI robots are not low cost. At least not optimized for cost.
Those robots are used as platform to experiment and develop state of the art research. For academia, it make much more sense to invest in quality sensor and cutting edge compact electronic that ease our life while experimenting.

I can understand how this can be frustrating from a hobbyist point of view, but I think you can find all the resources on this GitHub and in the forum to replace some components, design different actuators, etc.  Actually, you will find in the forum some threads about lower cost alternative to the choices made in the project.

About specific question / suggestion:

- Yes a low cost IMU could be used, with a more complex state estimation and calibration, but I would still expect a decrease of performances.
- The master-board is a compact design. Using a shield and standard dev board is possible but would take more space, In Solo12 we have very few margin. The Ethernet is a must to do high frequency feedback loop with a computer.
- The motor could be different, but some CAD adjustment are needed to accommodate with different size, and fixture.
- The cost is also due to the custom electronic to control the motor, Other lower cost project exist, but are not as compact nor adapted to our need.

Please understand that we would love to see spin-off of this project optimizing cost, exploring different design choices but we can not invest our work time to do it our-self.

I hope this helps,
Thomas.

MEE2022, 2022-11-08:
What is the estimated cost of the biped hardware (if you don't count the 3d printed parts)?

easybuildtech, 2022-11-24:
@MEE2022 I have been noting costs, on a BOM, as I build if it helps:  https://easybuildtech.com/open-dynamic-robot-initiative-bolt-cost-breakdown/

I am in the U.S.

MEE2022, 2022-11-24:
Thank you very much.  This is very detailed and extremely helpful.

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

fgrimminger, 2022-12-06:
@easybuildtech
Great! Thanks for sharing!

Closed 2022-12-06.

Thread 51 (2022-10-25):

What solidworks version did you use with quadruped_robot_12dof_v1.1

dvogureckiy99, 2022-10-25:
Sorry, I cannot open quadruped_robot_12dof_v1.1.
What solidworks version did you use with quadruped_robot_12dof_v1.1 file?

fgrimminger, 2022-10-26:
Hi, the cad files for the quadruped_robot_12dof_v1.1 were saved with Solidworks 2020.

dvogureckiy99, 2022-10-26:
Thank you very mush, I am already solved this problem by changing my current version to 2022.

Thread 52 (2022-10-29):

Lower leg and Resin Print Questions

MEE2022, 2022-10-29:
I'm about to FDM print the lower leg part in carbon fiber.  I see target weights for other parts to make sure the center of mass for the inertia control unit is correct. What infill % did you use to achieve 60g?  Should this be my only carbon fiber part as far as what is strictly necessary?   I would like to resin print the rest.  What is suggested?  What resin would you suggest?  I would like to use my Elegoo Saturn.  Thanks in advance.

EDIT:  I can't seem to delete this.  I was able to find the information I was looking for
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

fgrimminger, 2022-11-07:
o.k. - I'm glad that you found the information.
No reason to delete your post - we can just close the issue.
Good luck with your project.

Closed 2022-11-07.

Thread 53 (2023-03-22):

Help with the implementation of impedance control

Seerzy, 2023-03-22:
Dear experts,

I am currently working on a quadruped robotics project that shares similarities with the open dynamic robots. I would greatly appreciate it if you could provide me with some resources, such as sample code or valuable research papers, to use as a reference for implementing impedance control. Thank you in advance for your assistance.

Tom

majidkhadiv, 2023-03-22:
Hi,
Implementing impedance control for quadruped robots is quite a simple idea. One of the earliest work implementing it for legged robots is this paper https://journals.sagepub.com/doi/pdf/10.1177/02783640122067309. Same approach was used later on for different robots https://www.research-collection.ethz.ch/bitstream/handle/20.500.11850/62121/1/eth-7765-01.pdf and https://ieeexplore.ieee.org/stamp/stamp.jsp?arnumber=8594448 for instance. A similar approach is used for Solo in https://ieeexplore.ieee.org/iel7/7083369/7339444/09015985.pdf but the force distribution problem is solved using quadratic programming. Here you can also find some code for that https://github.com/machines-in-motion/mim_control/tree/main/demos.

Best,
Majid

Closed 2023-04-26.

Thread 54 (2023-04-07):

CAN bus vs SPI

ronzelver, 2023-04-07:
I noticed the Micro Driver board also supports CAN bus, why isn't this being used as communication with the main ESP32 controller. CAN bus supports up to 1Mb/s.

bryn51, 2023-04-24:
serial is simpler to develop and use. Can bus requires a library, and its a complex protocol.
But I too think it would be better.  If I get around to implementing my idea of refactoring the code into C++ then maybe I can look at that too.  Meanwhile soldiering on trying to source the arts.

thomasfla, 2023-05-09:
It's true that CAN can be easier to work with, especially for the wiring part (number of wires, noise immunity). However, it also has its limitations and this is why we decided to switch to SPI instead.

- The CAN frequency is limited to 1Mbps. In the ODRI project, we use SPI from 6 to 8Mbps.
- The protocol is half duplex (you can only exchange data in one direction) instead the SPI protocol we implemented is full duplex, so the effective bandwidth is doubled.
- The CAN frames need to be encapsulated with quite some overhead (address, framing header etc.)
- The CAN frames are very short (8Bytes) making the header overhead even more problematic.
- The addressing of CAN in not implemented yet in the uDriver (only one uDriver per CAN channel) and we have no manpower to work on this.

We are considering other solutions (CAN-FD, and RS485 at 20Mbps) with the new version of the motor drivers (still under test): https://github.com/open-dynamic-robot-initiative/open-motor-driver-initiative
It was not possible to implement this with the older electronics.

Sorry for entering so late in this conversation.
Best,
Thomas.

Closed 2023-07-24.

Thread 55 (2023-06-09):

Foot Sensor Voltage supply

Seerzy, 2023-06-09:
Hi Guys,

I am using the same feet design from open dynamic. It is very good, and perform very well.
However, my system only have 5V, can I use the same design but change the supply voltage from 3v3 to 5V.
I did some testing, 5V supply can work for short term, but I do not know whether it gonna affect the life span or not.

Tom

Seerzy, 2023-06-13:
Hi Guys,

I though it gonna be a problem coz the voltage of the LED sensor is meant to be 3.3V. Can someone help me verify whether I can use 5V to power the feet sensor system?

fgrimminger, 2023-06-13:
Hi Tom,

I'm glad to hear that the foot sensor works for your project.
I talked to Joshi Walzog, who had designed the board, regarding your question.

His only concern were the external indicator leds which get too much current at 5V and might get damaged over time (about 60mA instead of about 20mA).
So he recommends to increase the resistance of the resistors R1, R2, R6 and R7 to 150ohms (51ohms at the moment for 3.3V).
For keeping the light intensity of the internal led at the same level you could increase the resistor R8 to 4k ohms (560ohms at the moment for 3.3V) - that's optional and will depend on how you want to tune the sensor characteristics.

We designed the board for 3.3V because the ADC on our microcontroller can only handle up to 3.3V.
When you increase the voltage to 5V you need to make sure that your microcontroller can handle 5V on the inputs.

Below is the latest schematic for reference.

I hope that helps.
Best wishes. Felix

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

eijijiokk, 2023-06-27:
Dear Felix Grimminger,
Thank you for share your research work with the community. I would like to know if is possible to get the STEP files for the design of the actuator module shell cover, since there is an issue  to convert STL file to a mesh. It missed some parts of the design.
Thank you so much.

fgrimminger, 2023-06-27:
Hi,
sure - below is the upper leg shell base and cover in the STEP format.
Best. Felix

[upper_leg_module_step.zip](https://github.com/open-dynamic-robot-initiative/open_robot_actuator_hardware/files/11884271/upper_leg_module_step.zip)

fgrimminger, 2023-07-24:
Dear Eliana,
you're welcome!
Thank you and good luck with your project!
Best. Felix

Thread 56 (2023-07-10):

Dear my friends, I have some questions about your electronics part.

wangyear, 2023-07-10:
Excuse me, could you tell me what the software you have used to design your Micro Driver Electronics (pcb), looking forward to your replay. thank you very much.

nim65s, 2023-07-10:
Hi,

Our latest project use kicad, you'll find it here: https://github.com/open-dynamic-robot-initiative/power-board/tree/main/hardware

wangyear, 2023-07-10:
> Hi,
>
> Our latest project use kicad, you'll find it here: https://github.com/open-dynamic-robot-initiative/power-board/tree/main/hardware
Thank you very much, I will try it.

wangyear, 2023-07-20:
hi，please sign up your github account，i have some quessions about your project.Sorry to bother you.
---- Replied Message ----
| From | Guilhem ***@***.***> |
| Date | 07/10/2023 23:19 |
| To | open-dynamic-robot-initiative/open_robot_actuator_hardware ***@***.***> |
| Cc | wangyear ***@***.***>,
Author ***@***.***> |
| Subject | Re: [open-dynamic-robot-initiative/open_robot_actuator_hardware] Dear my friends, I have some questions about your electronics part. (Issue #56) |

Hi,

Our latest project use kicad, you'll find it here: https://github.com/open-dynamic-robot-initiative/power-board/tree/main/hardware

—
Reply to this email directly, view it on GitHub, or unsubscribe.
You are receiving this because you authored the thread.Message ID: ***@***.***>

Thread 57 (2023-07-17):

Dear my friends, i have some questions about your sensors used in your project.

wangyear, 2023-07-17:
I'm sorry to bother you to tell me that what the sensors you have used in your project, and its concrete information. Now i just found only one sensor used in your wheels, right? If you have used other sensors, please offer me the information. Thanks a lot, looking forward to your reply.

fgrimminger, 2023-07-24:
Hi,
for measuring the joint positions we use an optical encoder:
https://github.com/open-dynamic-robot-initiative/open_robot_actuator_hardware/blob/master/mechanics/actuator_module_v1/README.md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

The only other sensor that we are using is an IMU on the body of the robot:
https://github.com/open-dynamic-robot-initiative/open_robot_actuator_hardware/blob/master/mechanics/quadruped_robot_12dof_v1/README.md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

Best. Felix

wangyear, 2023-07-24:
Thank you so such.
---- Replied Message ----
| From | Felix ***@***.***> |
| Date | 07/24/2023 19:47 |
| To | ***@***.***> |
| Cc | WANGYI ***@***.***>,
Author ***@***.***> |
| Subject | Re: [open-dynamic-robot-initiative/open_robot_actuator_hardware] Dear my friends, i have some questions about your sensors used in your project. (Issue #57) |

Hi,
for measuring the joint positions we use an optical encoder:
https://github.com/open-dynamic-robot-initiative/open_robot_actuator_hardware/blob/master/mechanics/actuator_module_v1/README.md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

The only other sensor that we are using is an IMU on the body of the robot:
https://github.com/open-dynamic-robot-initiative/open_robot_actuator_hardware/blob/master/mechanics/quadruped_robot_12dof_v1/README.md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

Best. Felix

—
Reply to this email directly, view it on GitHub, or unsubscribe.
You are receiving this because you authored the thread.Message ID: ***@***.***>

fgrimminger, 2023-07-24:
You're welcome.
Thanks for your interest.
Best. Felix

Closed 2023-07-24.

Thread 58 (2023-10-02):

technical drawing of machined part motor shaft does not specify width of the flat rectangle

hzhaoc, 2023-10-02:
see https://github.com/open-dynamic-robot-initiative/open_robot_actuator_hardware/blob/master/mechanics/actuator_module_v1/drawings/motor_shaft.PDF

the flat rectangle:
-  length is 4.50mm
- depth into the cylinder is (3.99 - 3.40)/2 = 0.295mm
- distance from cylinder top is 1.50mm
- But I don't see the **width** of it. What value is it？

hzhaoc, 2023-10-02:
i saw the step files

Closed 2023-10-02.

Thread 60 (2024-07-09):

BOM and Eagle PCB File Mismatch

MATH-286-Pro, 2024-07-09:
Hello, I am a beginner in PCB design.

While reviewing the files for the Micro Driver on [this page](https://github.com/open-dynamic-robot-initiative/open_robot_actuator_hardware/tree/master/electronics/micro_driver_electronics), I noticed that in the Eagle design files, the values of components **C13, C14, C15, C49, C56, and C57** are listed as **2200p**, but in the BOM they are shown as **0.047uF**. Will this have a significant impact? Looking forward to your reply :)

_Screenshot in Eagle:_
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

_Screenshot in BOM: (The purple line)_
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

Closed 2024-07-17.

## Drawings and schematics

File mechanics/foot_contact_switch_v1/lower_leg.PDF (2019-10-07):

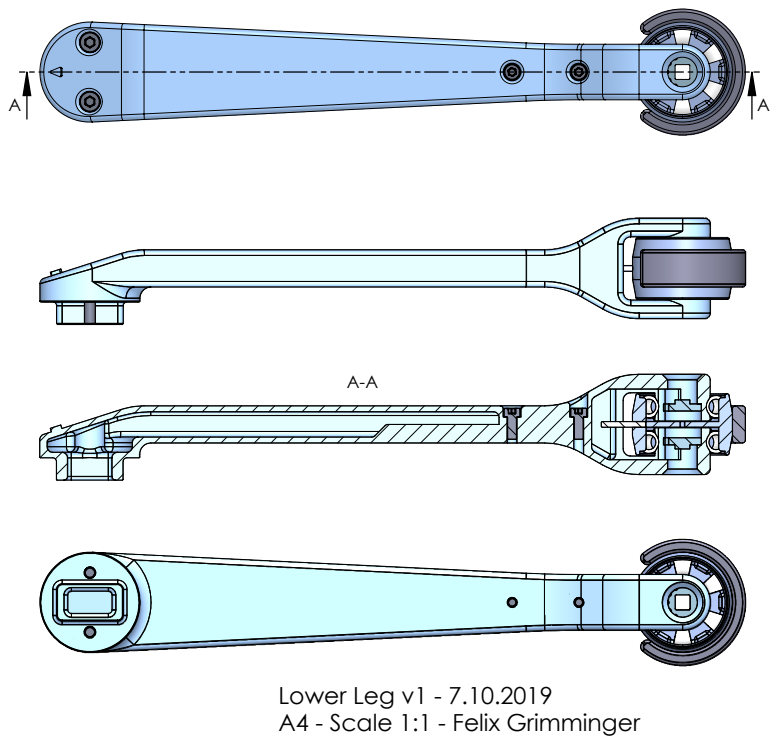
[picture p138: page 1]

Lower Leg v1 - 7.10.2019
A4 - Scale 1:1 - Felix Grimminger

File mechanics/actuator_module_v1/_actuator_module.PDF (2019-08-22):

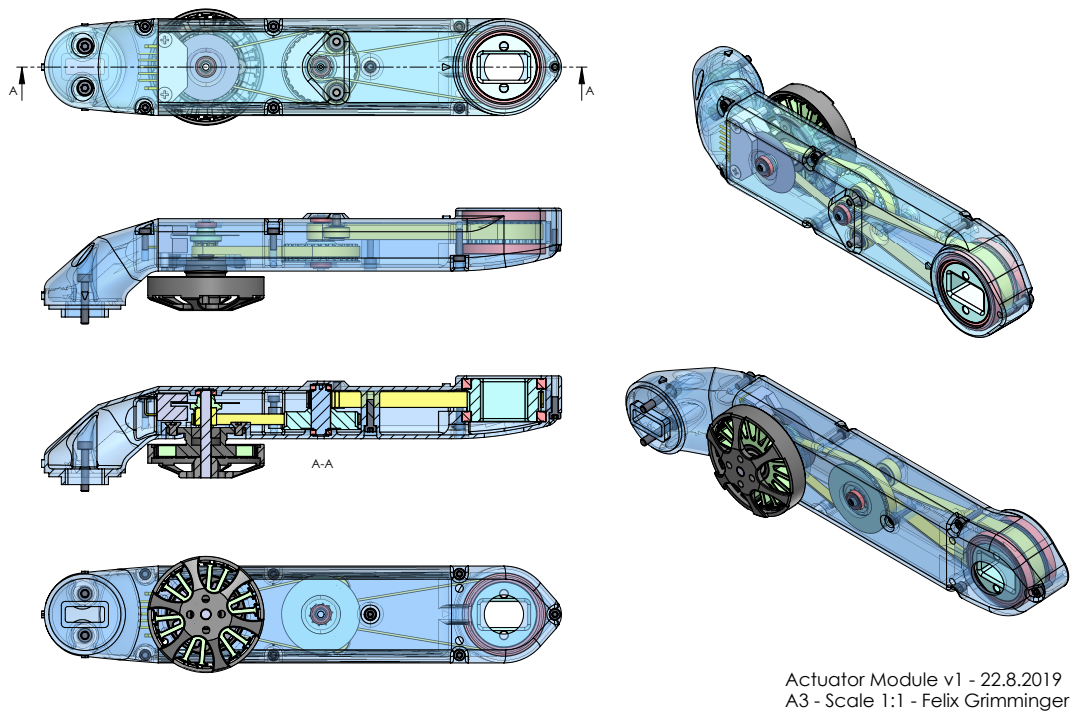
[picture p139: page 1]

Actuator Module v1 - 22.8.2019
A3 - Scale 1:1 - Felix Grimminger

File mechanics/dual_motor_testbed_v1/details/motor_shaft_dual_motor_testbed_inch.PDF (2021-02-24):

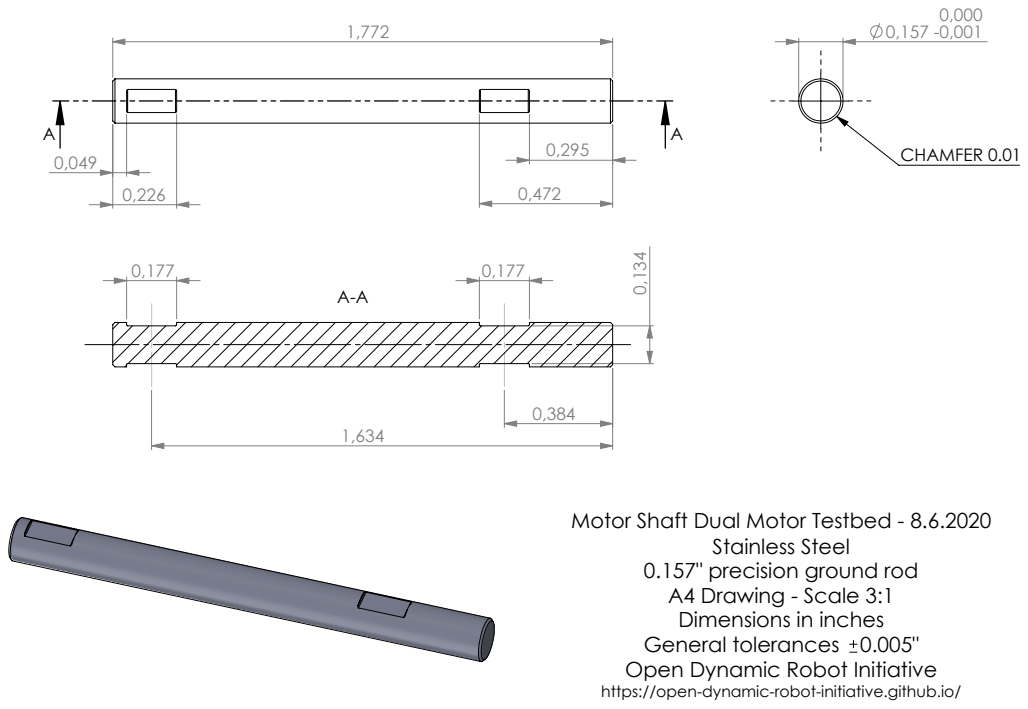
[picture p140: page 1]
CHAMFER 0.01; Stainless Steel; General tolerances

Motor Shaft Dual Motor Testbed - 8.6.2020
0.157" precision ground rod
A4 Drawing - Scale 3:1
Dimensions in inches
Open Dynamic Robot Initiative
https://open-dynamic-robot-initiative.github.io/

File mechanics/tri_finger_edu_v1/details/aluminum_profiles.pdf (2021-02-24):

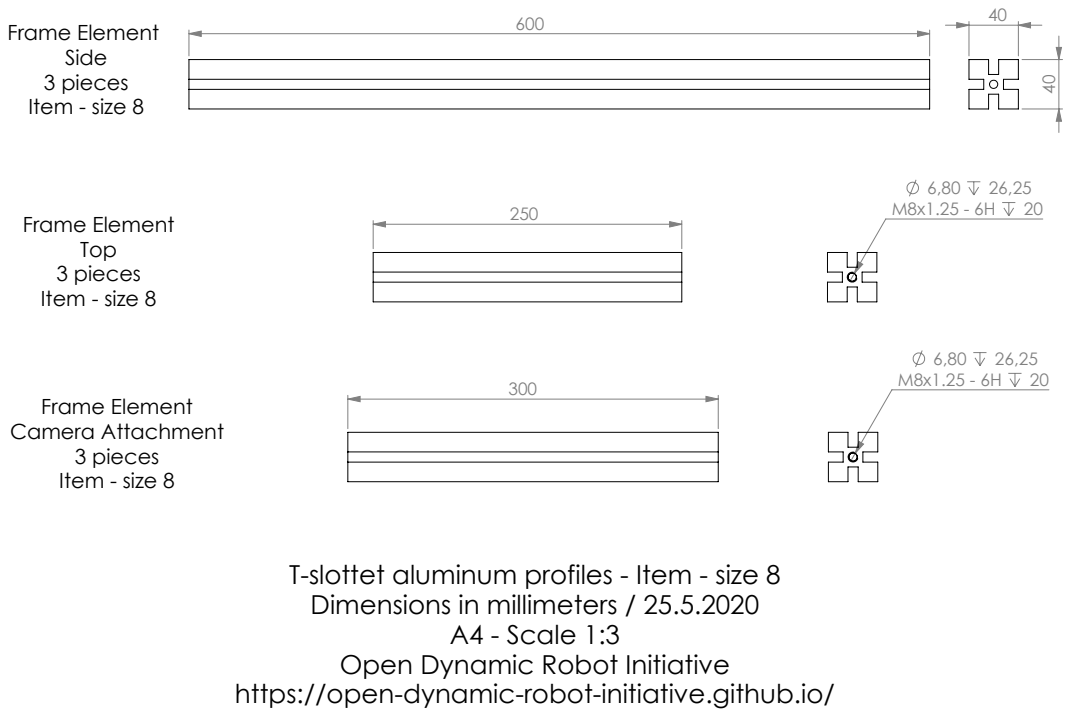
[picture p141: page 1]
600 Frame Element; 3 pieces Item - size 8; A4 - Scale 1:3; Frame Element; Frame Element Camera Attachment 3 pieces Item - size 8

T-slottet aluminum profiles - Item - size 8
Dimensions in millimeters / 25.5.2020
Open Dynamic Robot Initiative
https://open-dynamic-robot-initiative.github.io/

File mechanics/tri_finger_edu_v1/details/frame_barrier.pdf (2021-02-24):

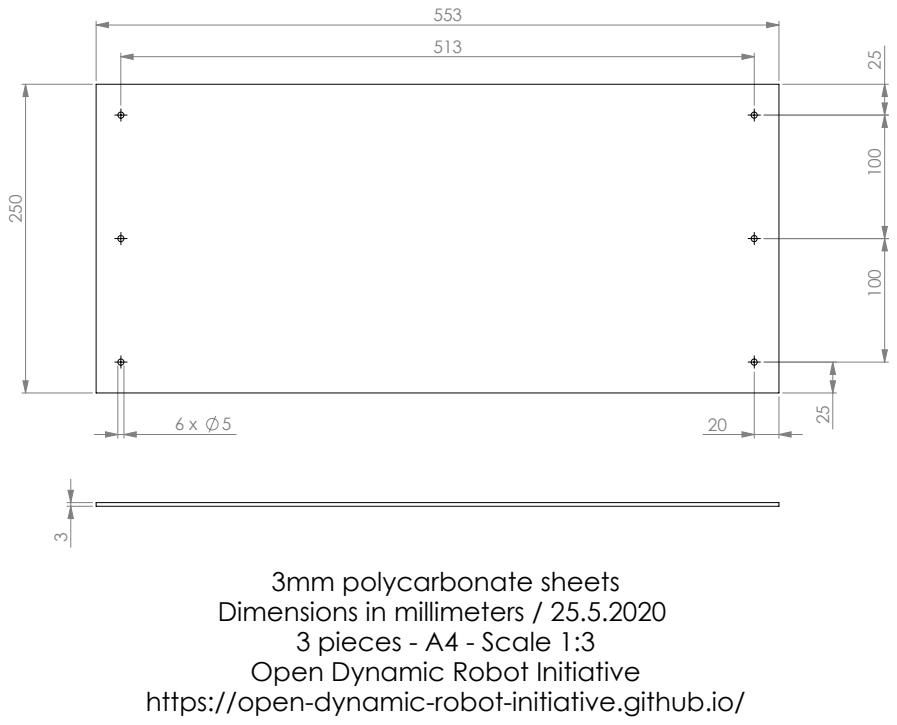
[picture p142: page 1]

3mm polycarbonate sheets
Dimensions in millimeters / 25.5.2020
3 pieces - A4 - Scale 1:3
Open Dynamic Robot Initiative
https://open-dynamic-robot-initiative.github.io/

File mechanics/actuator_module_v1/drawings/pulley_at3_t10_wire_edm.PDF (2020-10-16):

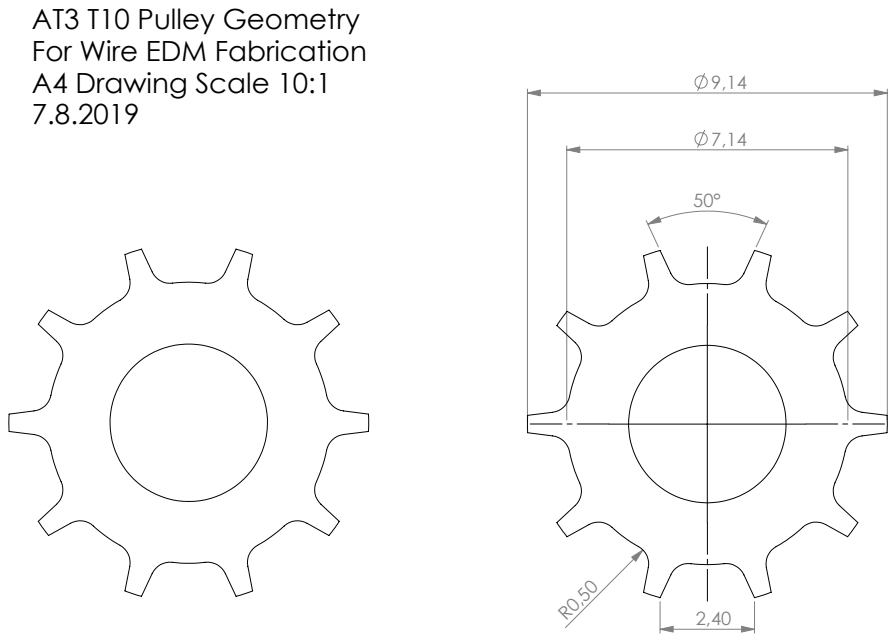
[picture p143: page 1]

AT3 T10 Pulley Geometry
For Wire EDM Fabrication
A4 Drawing Scale 10:1

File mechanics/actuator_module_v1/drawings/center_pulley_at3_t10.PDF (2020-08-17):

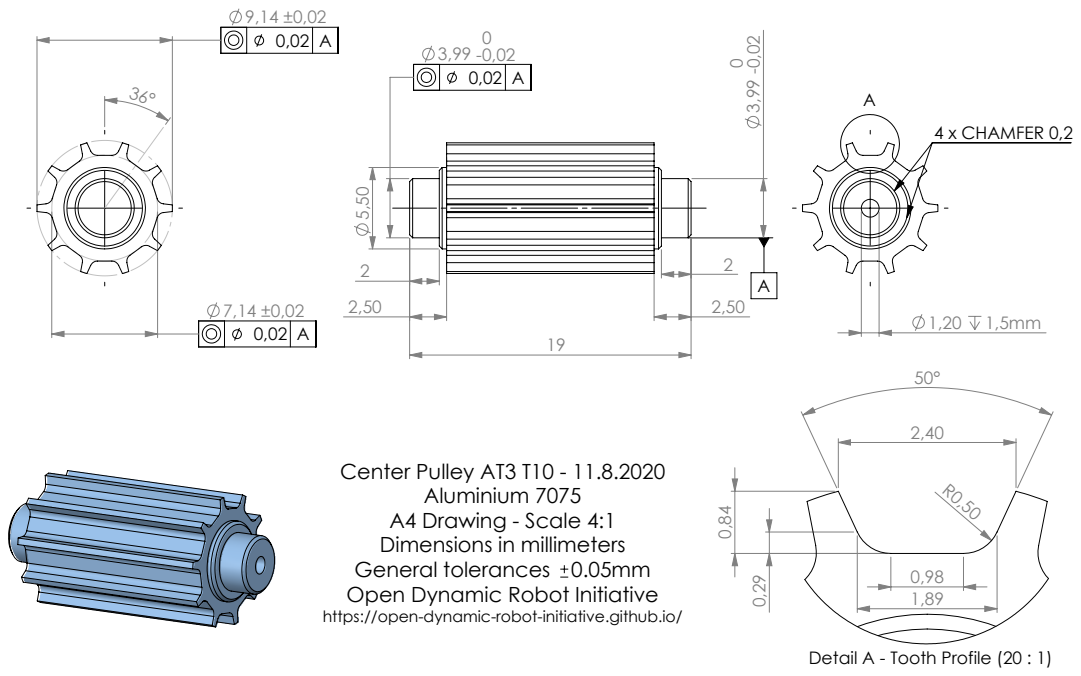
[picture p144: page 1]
4 x CHAMFER 0,2; General tolerances

Center Pulley AT3 T10 - 11.8.2020
Aluminium 7075
A4 Drawing - Scale 4:1
Dimensions in millimeters
Open Dynamic Robot Initiative
https://open-dynamic-robot-initiative.github.io/

Detail A - Tooth Profile (20 : 1)

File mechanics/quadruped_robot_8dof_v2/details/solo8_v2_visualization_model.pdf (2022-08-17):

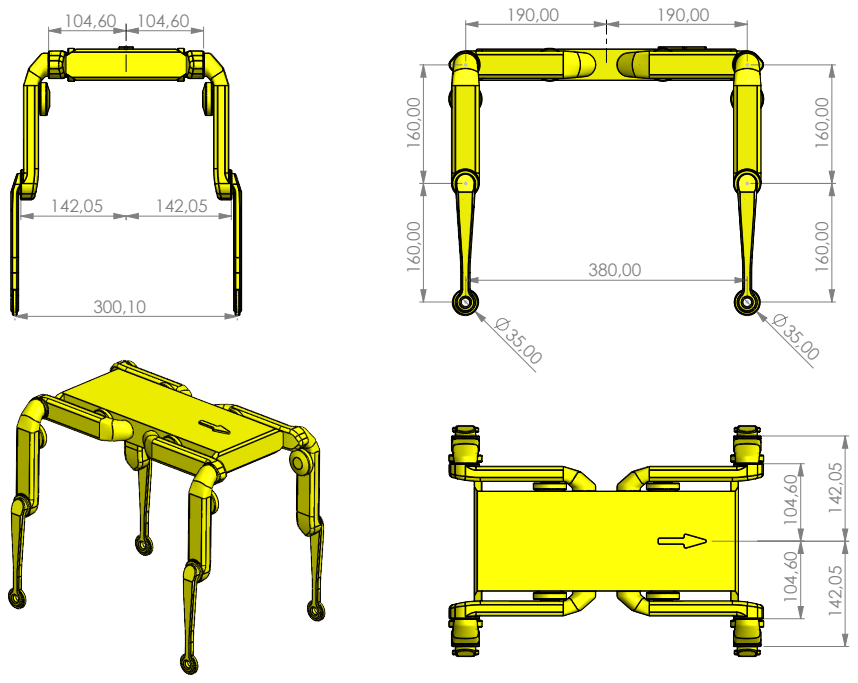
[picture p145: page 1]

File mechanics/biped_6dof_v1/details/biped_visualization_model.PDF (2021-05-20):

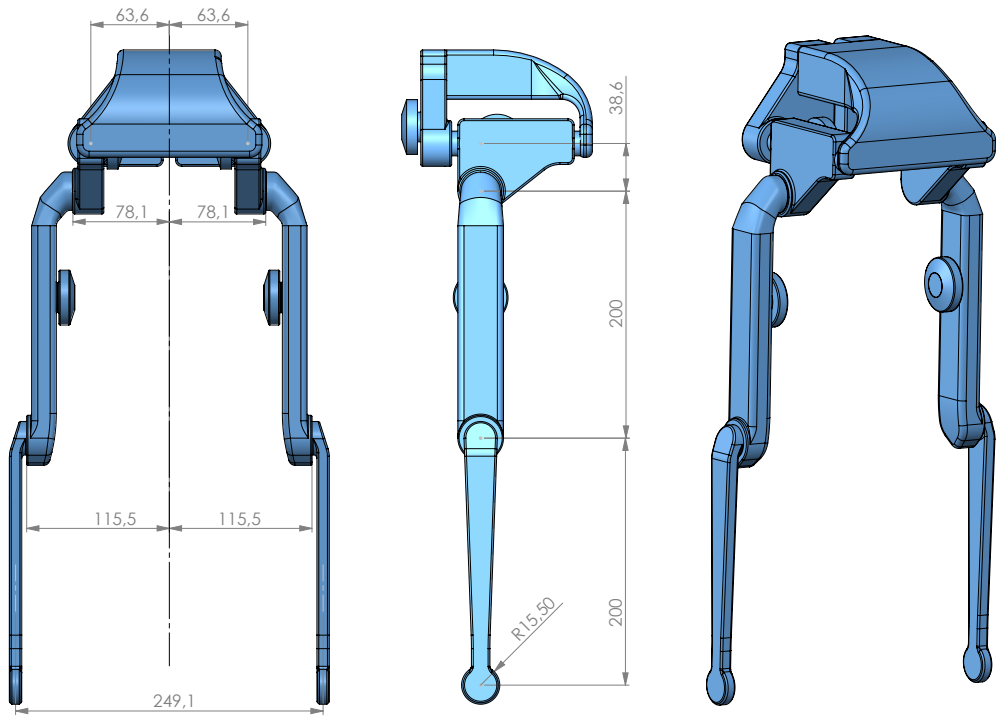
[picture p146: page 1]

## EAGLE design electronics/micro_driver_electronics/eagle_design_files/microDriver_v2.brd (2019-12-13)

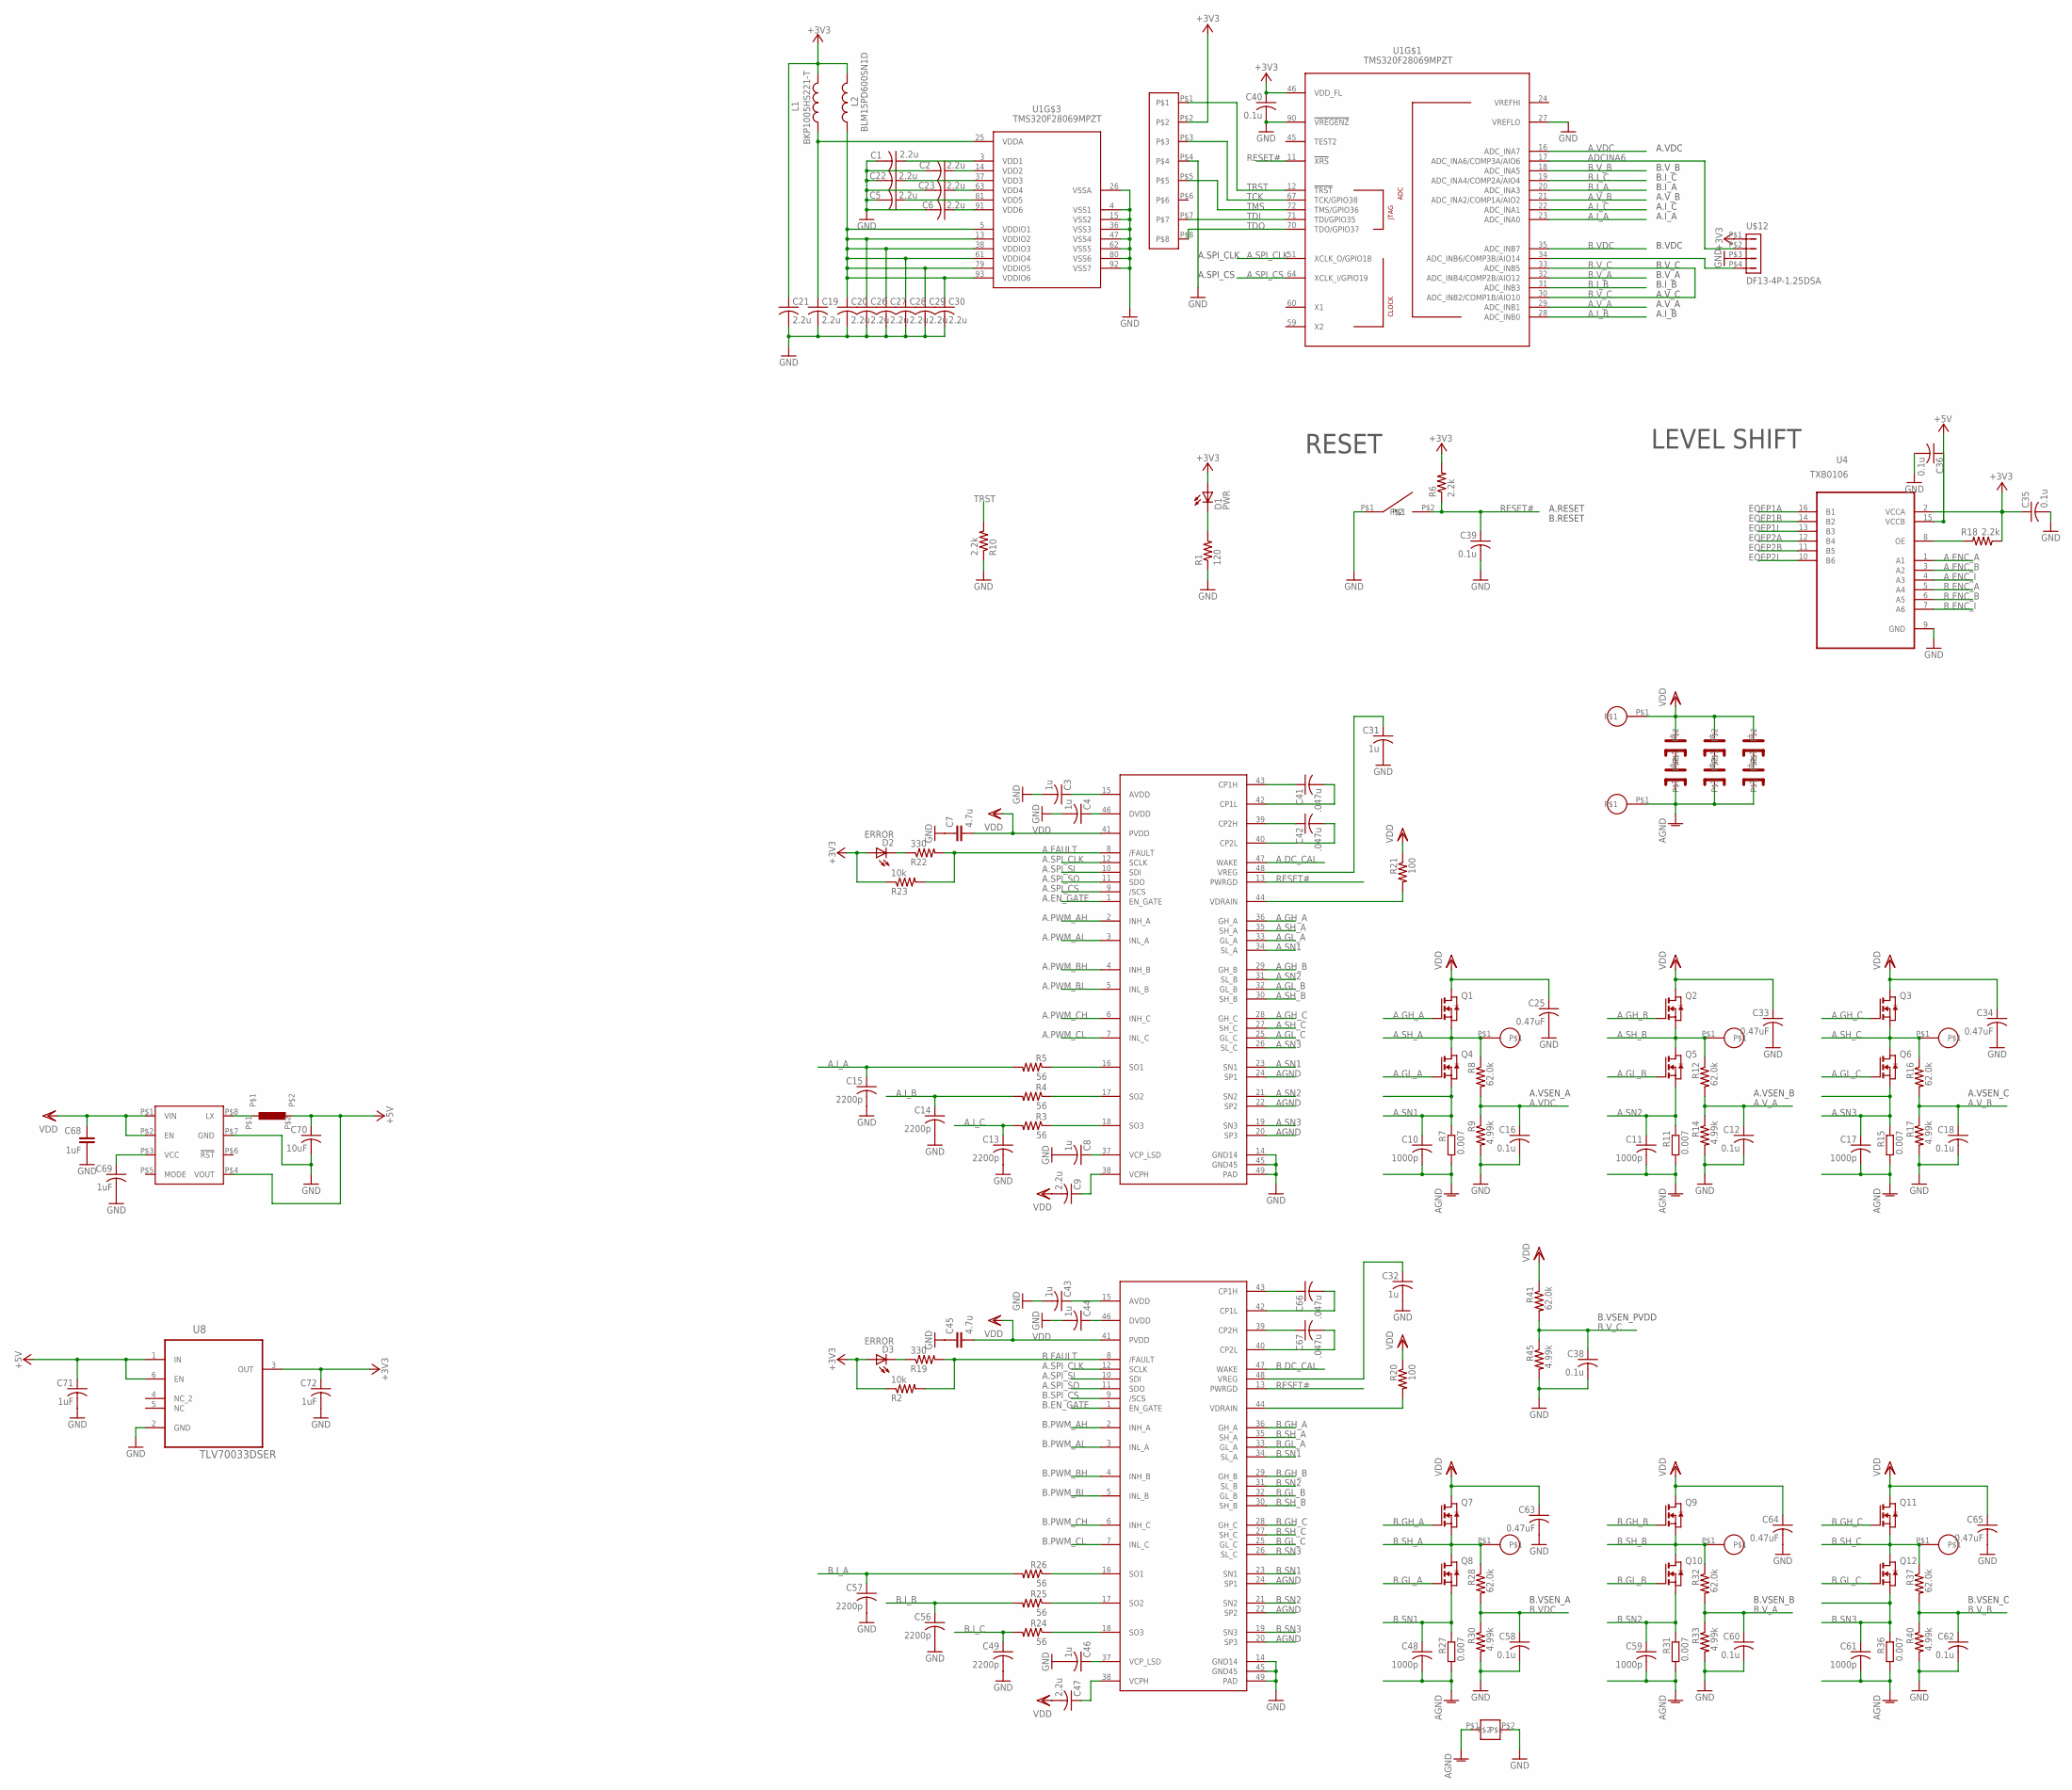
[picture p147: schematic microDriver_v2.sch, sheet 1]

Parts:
B1: B3U
C1, C2, C5, C6, C9, C19, C20, C21, C22, C23, C26, C27, C28, C29, C30, C47: 2.2u; C0402
C3, C4, C8, C31, C32, C43, C44, C46: 1u; C0402
C7, C45: 4.7u; C0805K
C10, C11, C17, C48, C59, C61: 1000p; C0402
C12, C16, C18, C35, C36, C38, C39, C40, C58, C60, C62: 0.1u; C0402
C13, C14, C15, C49, C56, C57: 2200p; C0402
C25, C33, C34, C63, C64, C65: 0.47uF; C0402
C41, C42, C66, C67: .047u; C0402
C68: 1uF; C0603
C69, C71, C72: 1uF; C0402
C70: 10uF; C0402
D1: PWR; CHIP-LED0603
D2, D3: ERROR; CHIP-LED0603
I1: NR4018; 4X4
L1: BKP1005HS221-T; R0402
L2: BLM15PD600SN1D; R0402
M1: AMP-8; AMP-MINITEK-8
Q1, Q2, Q3, Q4, Q5, Q6, Q7, Q8, Q9, Q10, Q11, Q12: CSD18540; Q5B
R1: 120; R0402
R2, R23: 10k; R0402
R3, R4, R5, R24, R25, R26: 56; R0402
R6, R10, R18: 2.2k; R0402
R7, R11, R15, R27, R31, R36: 0.007; R2512
R8, R12, R16, R28, R32, R37, R41: 62.0k; R0402
R9, R14, R17, R30, R33, R40, R45: 4.99k; R0402
R19, R22: 330; R0402
R20, R21: 100; R0402
T1, T2, T3, T4, T5, T6: 7343-CAP; M7343-CAP
U1: TMS320F28069MPZT; PQFP100
U4: TXB0106; VQFN-N16
U5, U6: DRV8305; HTQFP-48
U7: MAX15062; TDFN-8
U8: TLV70033DSER; SON50P150X150X80-6N
U$2: GND-AGND
U$3, U$4, U$5, U$6, U$7, U$8, U$9, U$10: BLDC_PAD
U$12: DF13-4P-1.25DSA

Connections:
+3V3: C21.1, C35.1, C40.1, C72.1, D1.A, D2.A, D3.A, L1.2, L2.2, M1.P$2, R2.1, R6.2, R18.1, R23.1, U1.46 (VDD_FL), U4.2 (VCCA), U8.3 (OUT), U$12.P$1 (1); also elsewhere on the board
+5V: C36.1, C70.1, C71.1, I1.P$2, U4.15 (VCCB), U7.P$4 (VOUT), U8.1 (IN), U8.6 (EN); also elsewhere on the board
A.DC_CAL: U6.47 (WAKE); also elsewhere on the board
A.ENC_A: U4.1 (A1); also elsewhere on the board
A.ENC_B: U4.3 (A2); also elsewhere on the board
A.ENC_I: U4.4 (A3); also elsewhere on the board
A.EN_GATE: U6.1 (EN_GATE); also elsewhere on the board
A.FAULT: R22.2, R23.2, U6.8 (/FAULT); also elsewhere on the board
A.GH_A: Q1.4 (G), U6.36 (GH_A)
A.GH_B: Q2.4 (G), U6.29 (GH_B)
A.GH_C: Q3.4 (G), U6.28 (GH_C)
A.GL_A: Q4.4 (G), U6.33 (GL_A)
A.GL_B: Q5.4 (G), U6.32 (GL_B)
A.GL_C: Q6.4 (G), U6.25 (GL_C)
A.I_A: C15.1, R5.2, U1.23 (ADC_INA0)
A.I_B: C14.1, R4.2, U1.28 (ADC_INB0)
A.I_C: C13.1, R3.2, U1.22 (ADC_INA1)
A.PWM_AH: U6.2 (INH_A); also elsewhere on the board
A.PWM_AL: U6.3 (INL_A); also elsewhere on the board
A.PWM_BH: U6.4 (INH_B); also elsewhere on the board
A.PWM_BL: U6.5 (INL_B); also elsewhere on the board
A.PWM_CH: U6.6 (INH_C); also elsewhere on the board
A.PWM_CL: U6.7 (INL_C); also elsewhere on the board
A.SH_A: Q1.1 (S), Q1.2 (S), Q1.3 (S), Q4.5 (D), Q4.6 (D), Q4.7 (D), Q4.8 (D), Q4.9 (D), R8.1, U6.35 (SH_A), U$6.P$1
A.SH_B: Q2.1 (S), Q2.2 (S), Q2.3 (S), Q5.5 (D), Q5.6 (D), Q5.7 (D), Q5.8 (D), Q5.9 (D), R12.1, U6.30 (SH_B), U$7.P$1
A.SH_C: Q3.1 (S), Q3.2 (S), Q3.3 (S), Q6.5 (D), Q6.6 (D), Q6.7 (D), Q6.8 (D), Q6.9 (D), R16.1, U6.27 (SH_C), U$8.P$1
A.SN1: C10.1, Q4.1 (S), Q4.2 (S), Q4.3 (S), R7.1, U6.23 (SN1), U6.34 (SL_A)
A.SN2: C11.1, Q5.1 (S), Q5.2 (S), Q5.3 (S), R11.1, U6.21 (SN2), U6.31 (SL_B)
A.SN3: C17.1, Q6.1 (S), Q6.2 (S), Q6.3 (S), R15.1, U6.19 (SN3), U6.26 (SL_C)
A.SPI_CLK: U1.51 (XCLK_O/GPIO18), U5.12 (SCLK), U6.12 (SCLK); also elsewhere on the board
A.SPI_CS: U1.64 (XCLK_I/GPIO19), U6.9 (/SCS)
A.SPI_SI: U5.10 (SDI), U6.10 (SDI); also elsewhere on the board
A.SPI_SO: U5.11 (SDO), U6.11 (SDO); also elsewhere on the board
A.VDC: C16.1, R8.2, R9.1, U1.16 (ADC_INA7)
A.V_A: C12.1, R12.2, R14.1, U1.29 (ADC_INB1)
A.V_B: C18.1, R16.2, R17.1, U1.21 (ADC_INA2/COMP1A/AIO2)
ADCINA6: U1.17 (ADC_INA6/COMP3A/AIO6), U$12.P$2 (2)
AGND: C10.2, C11.2, C17.2, C48.2, C59.2, C61.2, R7.2, R11.2, R15.2, R27.2, R31.2, R36.2, T2.-, T4.-, T6.-, U5.20 (SP3), U5.22 (SP2), U5.24 (SP1), U6.20 (SP3), U6.22 (SP2), U6.24 (SP1), U$2.P$1, U$10.P$1
AVDD: C3.1, U6.15 (AVDD)
AVDD1: C43.1, U5.15 (AVDD)
B.DC_CAL: U5.47 (WAKE); also elsewhere on the board
B.ENC_A: U4.5 (A4); also elsewhere on the board
B.ENC_B: U4.6 (A5); also elsewhere on the board
B.ENC_I: U4.7 (A6); also elsewhere on the board
B.EN_GATE: U5.1 (EN_GATE); also elsewhere on the board
B.FAULT: R2.2, R19.2, U5.8 (/FAULT); also elsewhere on the board
B.GH_A: Q7.4 (G), U5.36 (GH_A)
B.GH_B: Q9.4 (G), U5.29 (GH_B)
B.GH_C: Q11.4 (G), U5.28 (GH_C)
B.GL_A: Q8.4 (G), U5.33 (GL_A)
B.GL_B: Q10.4 (G), U5.32 (GL_B)
B.GL_C: Q12.4 (G), U5.25 (GL_C)
B.I_A: C57.1, R26.2, U1.20 (ADC_INA3)
B.I_B: C56.1, R25.2, U1.31 (ADC_INB3)
B.I_C: C49.1, R24.2, U1.19 (ADC_INA4/COMP2A/AIO4)
B.PWM_AH: U5.2 (INH_A); also elsewhere on the board
B.PWM_AL: U5.3 (INL_A); also elsewhere on the board
B.PWM_BH: U5.4 (INH_B); also elsewhere on the board
B.PWM_BL: U5.5 (INL_B); also elsewhere on the board
B.PWM_CH: U5.6 (INH_C); also elsewhere on the board
B.PWM_CL: U5.7 (INL_C); also elsewhere on the board
B.SH_A: Q7.1 (S), Q7.2 (S), Q7.3 (S), Q8.5 (D), Q8.6 (D), Q8.7 (D), Q8.8 (D), Q8.9 (D), R28.1, U5.35 (SH_A), U$3.P$1
B.SH_B: Q9.1 (S), Q9.2 (S), Q9.3 (S), Q10.5 (D), Q10.6 (D), Q10.7 (D), Q10.8 (D), Q10.9 (D), R32.1, U5.30 (SH_B), U$4.P$1
B.SH_C: Q11.1 (S), Q11.2 (S), Q11.3 (S), Q12.5 (D), Q12.6 (D), Q12.7 (D), Q12.8 (D), Q12.9 (D), R37.1, U5.27 (SH_C), U$5.P$1
B.SN1: C48.1, Q8.1 (S), Q8.2 (S), Q8.3 (S), R27.1, U5.23 (SN1), U5.34 (SL_A)
B.SN2: C59.1, Q10.1 (S), Q10.2 (S), Q10.3 (S), R31.1, U5.21 (SN2), U5.31 (SL_B)
B.SN3: C61.1, Q12.1 (S), Q12.2 (S), Q12.3 (S), R36.1, U5.19 (SN3), U5.26 (SL_C)
B.SPI_CS: U5.9 (/SCS); also elsewhere on the board
B.VDC: C58.1, R28.2, R30.1, U1.35 (ADC_INB7)
B.V_A: C60.1, R32.2, R33.1, U1.32 (ADC_INB4/COMP2B/AIO12)
B.V_B: C62.1, R37.2, R40.1, U1.18 (ADC_INA5)
B.V_C: C38.1, R41.2, R45.1, U1.30 (ADC_INB2/COMP1B/AIO10), U1.33 (ADC_INB5)
EQEP1A: U4.16 (B1); also elsewhere on the board
EQEP1B: U4.14 (B2); also elsewhere on the board
EQEP1I: U4.13 (B3); also elsewhere on the board
EQEP2A: U4.12 (B4); also elsewhere on the board
EQEP2B: U4.11 (B5); also elsewhere on the board
EQEP2I: U4.10 (B6); also elsewhere on the board
GND: B1.P$1, C1.2, C2.2, C3.2, C4.2, C5.2, C6.2, C7.1, C8.2, C12.2, C13.2, C14.2, C15.2, C16.2, C18.2, C19.2, C20.2, C21.2, C22.2, C23.2, C25.2, C26.2, C27.2, C28.2, C29.2, C30.2, C31.2, C32.2, C33.2, C34.2, C35.2, C36.2, C38.2, C39.2, C40.2, C43.2, C44.2, C45.1, C46.2, C49.2, C56.2, C57.2, C58.2, C60.2, C62.2, C63.2, C64.2, C65.2, C68.2, C69.2, C70.2, C71.2, C72.2, M1.P$4, R1.1, R9.2, R10.1, R14.2, R17.2, R30.2, R33.2, R40.2, R45.2, U1.4 (VSS1), U1.15 (VSS2), U1.26 (VSSA), U1.27 (VREFLO), U1.36 (VSS3), U1.47 (VSS4), U1.62 (VSS5), U1.80 (VSS6), U1.90 (!VREGENZ), U1.92 (VSS7), U4.9 (GND), U5.14 (GND14), U5.45 (GND45), U5.49 (PAD), U6.14 (GND14), U6.45 (GND45), U6.49 (PAD), U7.P$7 (GND), U8.2 (GND), U$2.P$2, U$12.P$3 (3); also elsewhere on the board
unnamed: U1.34 (ADC_INB6/COMP3B/AIO14), U$12.P$4 (4)
unnamed: C4.1, U6.46 (DVDD)
unnamed: R3.1, U6.18 (SO3)
unnamed: C8.1, U6.37 (VCP_LSD)
unnamed: C9.1, U6.38 (VCPH)
unnamed: C41.1, U6.43 (CP1H)
unnamed: R4.1, U6.17 (SO2)
unnamed: R5.1, U6.16 (SO1)
unnamed: C42.1, U6.39 (CP2H)
unnamed: C41.2, U6.42 (CP1L)
unnamed: C42.2, U6.40 (CP2L)
unnamed: R18.2, U4.8 (OE)
unnamed: D2.C, R22.1
unnamed: R21.2, U6.44 (VDRAIN)
unnamed: C44.1, U5.46 (DVDD)
unnamed: C46.1, U5.37 (VCP_LSD)
unnamed: C32.1, U5.48 (VREG)
unnamed: R24.1, U5.18 (SO3)
unnamed: C47.1, U5.38 (VCPH)
unnamed: R25.1, U5.17 (SO2)
unnamed: R26.1, U5.16 (SO1)
unnamed: C66.1, U5.43 (CP1H)
unnamed: C67.1, U5.39 (CP2H)
unnamed: C66.2, U5.42 (CP1L)
unnamed: C67.2, U5.40 (CP2L)
unnamed: D1.C, R1.2
unnamed: C1.1, U1.3 (VDD1)
unnamed: C2.1, U1.14 (VDD2)
unnamed: C22.1, U1.37 (VDD3)
unnamed: C23.1, U1.63 (VDD4)
unnamed: T1.-, T2.+
unnamed: T3.-, T4.+
unnamed: R20.2, U5.44 (VDRAIN)
unnamed: C5.1, U1.81 (VDD5)
unnamed: C6.1, U1.91 (VDD6)
unnamed: D3.C, R19.1
unnamed: T5.-, T6.+
unnamed: C31.1, U6.48 (VREG)
unnamed: I1.P$1, U7.P$8 (LX)
unnamed: C69.1, U7.P$3 (VCC)
RESET#: B1.P$2, C39.1, R6.1, U1.11 (!XRS), U5.13 (PWRGD), U6.13 (PWRGD)
TCK: M1.P$3, U1.67 (TCK/GPIO38)
TDI: M1.P$7, U1.71 (TDI/GPIO35)
TDO: M1.P$8, U1.70 (TDO/GPIO37)
TMS: M1.P$5, U1.72 (TMS/GPIO36)
TRST: M1.P$1, R10.2, U1.12 (!TRST)
VDD: C7.2, C9.2, C25.1, C33.1, C34.1, C45.2, C47.2, C63.1, C64.1, C65.1, C68.1, Q1.5 (D), Q1.6 (D), Q1.7 (D), Q1.8 (D), Q1.9 (D), Q2.5 (D), Q2.6 (D), Q2.7 (D), Q2.8 (D), Q2.9 (D), Q3.5 (D), Q3.6 (D), Q3.7 (D), Q3.8 (D), Q3.9 (D), Q7.5 (D), Q7.6 (D), Q7.7 (D), Q7.8 (D), Q7.9 (D), Q9.5 (D), Q9.6 (D), Q9.7 (D), Q9.8 (D), Q9.9 (D), Q11.5 (D), Q11.6 (D), Q11.7 (D), Q11.8 (D), Q11.9 (D), R20.1, R21.1, R41.1, T1.+, T3.+, T5.+, U5.41 (PVDD), U6.41 (PVDD), U7.P$1 (VIN), U7.P$2 (EN), U$9.P$1
VDDA: C19.1, L1.1, U1.25 (VDDA)
VDDIO: C20.1, C26.1, C27.1, C28.1, C29.1, C30.1, L2.1, U1.5 (VDDIO1), U1.13 (VDDIO2), U1.38 (VDDIO3), U1.61 (VDDIO4), U1.79 (VDDIO5), U1.93 (VDDIO6)

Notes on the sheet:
RESET
A.SPI_CLK
A.SPI_CS
A.RESET
B.RESET
B.VDC
B.V_A
B.V_B
B.V_C
B.I_A
B.I_B
B.I_C
A.VDC
A.V_A
A.V_B
A.V_C
A.I_A
A.I_B
A.I_C
A.VSEN_A
A.VSEN_B
A.VSEN_C
B.VSEN_A
B.VSEN_B
B.VSEN_C
B.VSEN_PVDD
LEVEL SHIFT

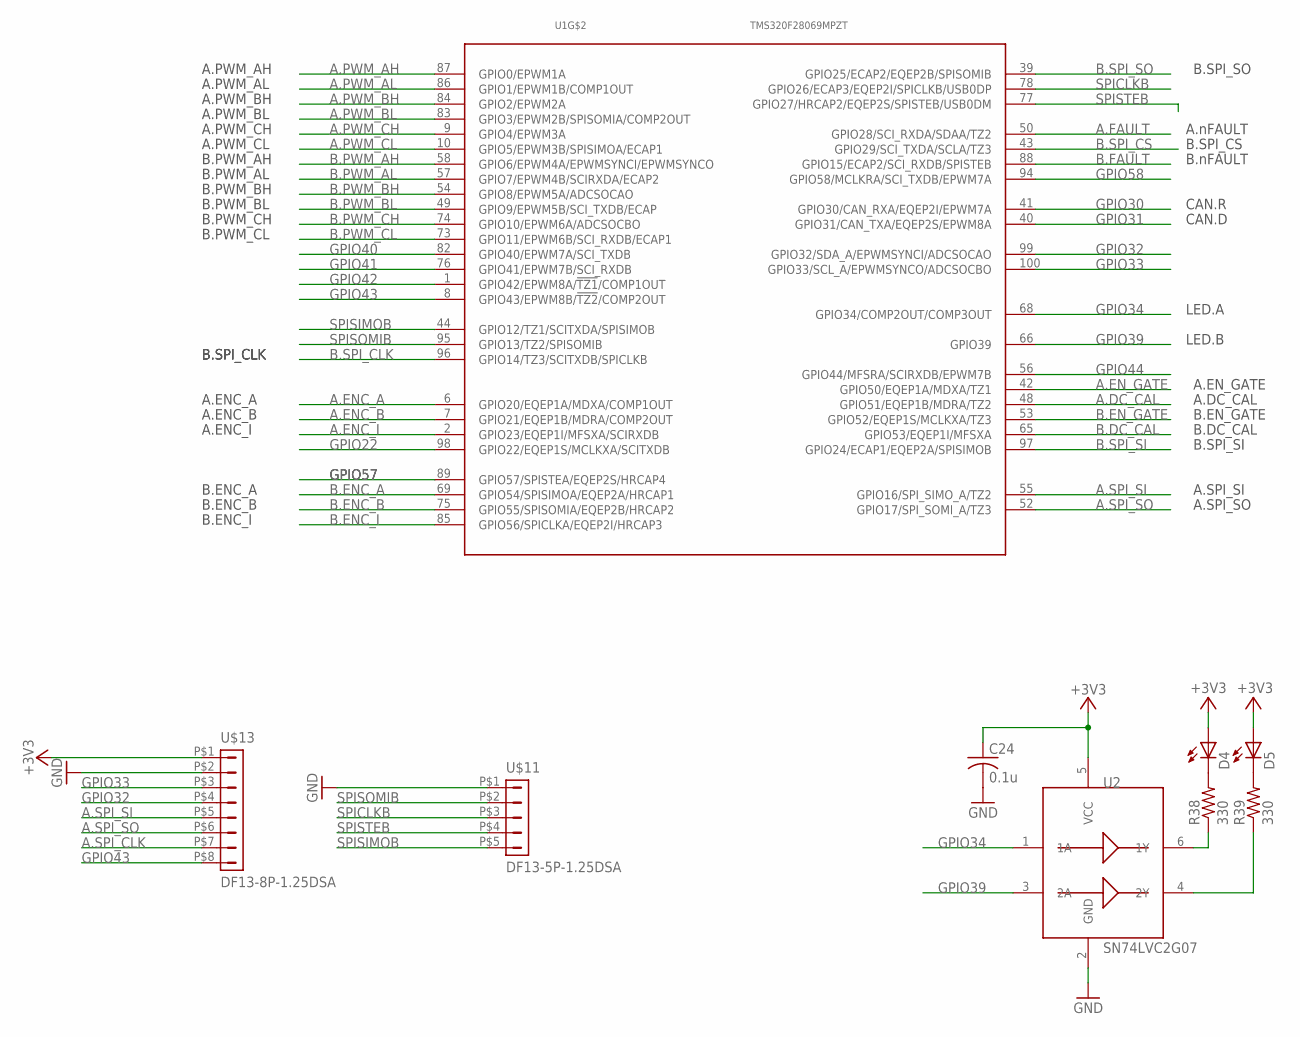
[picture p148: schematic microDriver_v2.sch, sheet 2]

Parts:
C24: 0.1u; C0402
D4, D5: LEDCHIP-LED0603; CHIP-LED0603
R38, R39: 330; R0402
U1: TMS320F28069MPZT; PQFP100
U2: SN74LVC2G07; SOT23-6-DBV
U$11: DF13-5P-1.25DSA
U$13: DF13-8P-1.25DSA

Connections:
+3V3: C24.1, D4.A, D5.A, U2.5 (VCC), U$13.P$1 (1); also elsewhere on the board
A.DC_CAL: U1.48 (GPIO51/EQEP1B/MDRA/TZ2); also elsewhere on the board
A.ENC_A: U1.6 (GPIO20/EQEP1A/MDXA/COMP1OUT); also elsewhere on the board
A.ENC_B: U1.7 (GPIO21/EQEP1B/MDRA/COMP2OUT); also elsewhere on the board
A.ENC_I: U1.2 (GPIO23/EQEP1I/MFSXA/SCIRXDB); also elsewhere on the board
A.EN_GATE: U1.42 (GPIO50/EQEP1A/MDXA/TZ1); also elsewhere on the board
A.FAULT: U1.50 (GPIO28/SCI_RXDA/SDAA/TZ2); also elsewhere on the board
A.PWM_AH: U1.87 (GPIO0/EPWM1A); also elsewhere on the board
A.PWM_AL: U1.86 (GPIO1/EPWM1B/COMP1OUT); also elsewhere on the board
A.PWM_BH: U1.84 (GPIO2/EPWM2A); also elsewhere on the board
A.PWM_BL: U1.83 (GPIO3/EPWM2B/SPISOMIA/COMP2OUT); also elsewhere on the board
A.PWM_CH: U1.9 (GPIO4/EPWM3A); also elsewhere on the board
A.PWM_CL: U1.10 (GPIO5/EPWM3B/SPISIMOA/ECAP1); also elsewhere on the board
A.SPI_CLK: U$13.P$7 (7); also elsewhere on the board
A.SPI_SI: U1.55 (GPIO16/SPI_SIMO_A/TZ2), U$13.P$5 (5); also elsewhere on the board
A.SPI_SO: U1.52 (GPIO17/SPI_SOMI_A/TZ3), U$13.P$6 (6); also elsewhere on the board
B.DC_CAL: U1.65 (GPIO53/EQEP1I/MFSXA); also elsewhere on the board
B.ENC_A: U1.69 (GPIO54/SPISIMOA/EQEP2A/HRCAP1); also elsewhere on the board
B.ENC_B: U1.75 (GPIO55/SPISOMIA/EQEP2B/HRCAP2); also elsewhere on the board
B.ENC_I: U1.85 (GPIO56/SPICLKA/EQEP2I/HRCAP3); also elsewhere on the board
B.EN_GATE: U1.53 (GPIO52/EQEP1S/MCLKXA/TZ3); also elsewhere on the board
B.FAULT: U1.88 (GPIO15/ECAP2/SCI_RXDB/SPISTEB); also elsewhere on the board
B.PWM_AH: U1.58 (GPIO6/EPWM4A/EPWMSYNCI/EPWMSYNCO); also elsewhere on the board
B.PWM_AL: U1.57 (GPIO7/EPWM4B/SCIRXDA/ECAP2); also elsewhere on the board
B.PWM_BH: U1.54 (GPIO8/EPWM5A/ADCSOCAO); also elsewhere on the board
B.PWM_BL: U1.49 (GPIO9/EPWM5B/SCI_TXDB/ECAP); also elsewhere on the board
B.PWM_CH: U1.74 (GPIO10/EPWM6A/ADCSOCBO); also elsewhere on the board
B.PWM_CL: U1.73 (GPIO11/EPWM6B/SCI_RXDB/ECAP1); also elsewhere on the board
B.SPI_CLK: U1.96 (GPIO14/TZ3/SCITXDB/SPICLKB)
B.SPI_CS: U1.43 (GPIO29/SCI_TXDA/SCLA/TZ3); also elsewhere on the board
B.SPI_SI: U1.97 (GPIO24/ECAP1/EQEP2A/SPISIMOB)
B.SPI_SO: U1.39 (GPIO25/ECAP2/EQEP2B/SPISOMIB)
GND: C24.2, U2.2 (GND), U$11.P$1 (1), U$13.P$2 (2); also elsewhere on the board
GPIO22: U1.98 (GPIO22/EQEP1S/MCLKXA/SCITXDB)
GPIO30: U1.41 (GPIO30/CAN_RXA/EQEP2I/EPWM7A); also elsewhere on the board
GPIO31: U1.40 (GPIO31/CAN_TXA/EQEP2S/EPWM8A); also elsewhere on the board
GPIO32: U1.99 (GPIO32/SDA_A/EPWMSYNCI/ADCSOCAO), U$13.P$4 (4)
GPIO33: U1.100 (GPIO33/SCL_A/EPWMSYNCO/ADCSOCBO), U$13.P$3 (3)
GPIO34: U1.68 (GPIO34/COMP2OUT/COMP3OUT), U2.1 (1A)
GPIO39: U1.66 (GPIO39), U2.3 (2A)
GPIO40: U1.82 (GPIO40/EPWM7A/SCI_TXDB)
GPIO41: U1.76 (GPIO41/EPWM7B/SCI_RXDB)
GPIO42: U1.1 (GPIO42/EPWM8A/!TZ1!/COMP1OUT)
GPIO43: U1.8 (GPIO43/EPWM8B/!TZ2!/COMP2OUT), U$13.P$8 (8)
GPIO44: U1.56 (GPIO44/MFSRA/SCIRXDB/EPWM7B)
GPIO57: U1.89 (GPIO57/SPISTEA/EQEP2S/HRCAP4)
GPIO58: U1.94 (GPIO58/MCLKRA/SCI_TXDB/EPWM7A)
unnamed: D4.C, R38.2
unnamed: D5.C, R39.2
unnamed: R38.1, U2.6 (1Y)
unnamed: R39.1, U2.4 (2Y)
SPICLKB: U1.78 (GPIO26/ECAP3/EQEP2I/SPICLKB/USB0DP), U$11.P$3 (3)
SPISIMOB: U1.44 (GPIO12/TZ1/SCITXDA/SPISIMOB), U$11.P$5 (5)
SPISOMIB: U1.95 (GPIO13/TZ2/SPISOMIB), U$11.P$2 (2)
SPISTEB: U1.77 (GPIO27/HRCAP2/EQEP2S/SPISTEB/USB0DM), U$11.P$4 (4)

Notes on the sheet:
A.nFAULT
B.nFAULT
B.SPI_CLK
B.PWM_AH
B.PWM_AL
B.PWM_BH
B.PWM_BL
B.PWM_CH
B.PWM_CL
A.PWM_AH
A.PWM_AL
A.PWM_BH
A.PWM_BL
A.PWM_CH
A.PWM_CL
B.SPI_CS
B.SPI_SI
B.SPI_SO
B.EN_GATE
B.DC_CAL
A.EN_GATE
A.DC_CAL
A.SPI_SI
A.SPI_SO
A.ENC_A
A.ENC_B
A.ENC_I
B.ENC_A
B.ENC_B
B.ENC_I
CAN.R
CAN.D
LED.A
LED.B

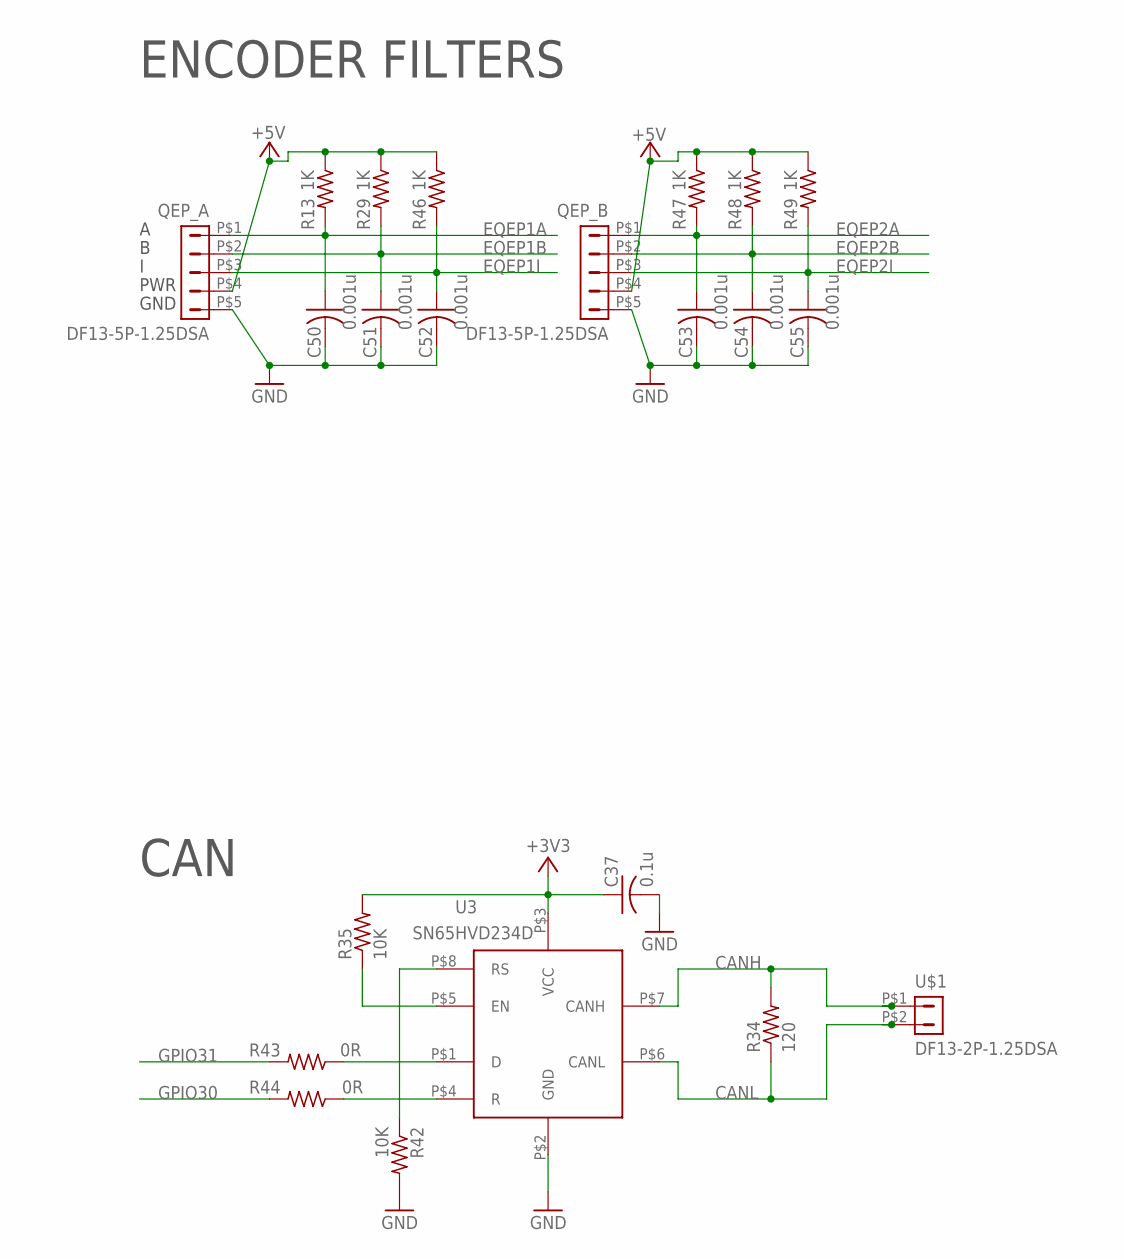
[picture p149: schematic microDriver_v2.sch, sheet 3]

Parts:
C37: 0.1u; C0402
C50, C51, C52, C53, C54, C55: 0.001u; C0402
QEP_A: DF13-5P-1.25DSA
QEP_B: DF13-5P-1.25DSA
R13, R29, R46, R47, R48, R49: 1K; R0402
R34: 120; R0402
R35, R42: 10K; R0402
R43, R44: 0R; R0402
U3: SN65HVD234D; SOIC8-PDSO
U$1: DF13-2P-1.25DSA

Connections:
+3V3: C37.1, R35.2, U3.P$3 (VCC); also elsewhere on the board
+5V: QEP_A.P$4 (4), QEP_B.P$4 (4), R13.1, R29.1, R46.1, R47.1, R48.1, R49.1; also elsewhere on the board
CANH: R34.2, U3.P$7 (CANH), U$1.P$1 (1)
CANL: R34.1, U3.P$6 (CANL), U$1.P$2 (2)
EQEP1A: C50.1, QEP_A.P$1 (1), R13.2; also elsewhere on the board
EQEP1B: C51.1, QEP_A.P$2 (2), R29.2; also elsewhere on the board
EQEP1I: C52.1, QEP_A.P$3 (3), R46.2; also elsewhere on the board
EQEP2A: C53.1, QEP_B.P$1 (1), R47.2; also elsewhere on the board
EQEP2B: C54.1, QEP_B.P$2 (2), R48.2; also elsewhere on the board
EQEP2I: C55.1, QEP_B.P$3 (3), R49.2; also elsewhere on the board
GND: C37.2, C50.2, C51.2, C52.2, C53.2, C54.2, C55.2, QEP_A.P$5 (5), QEP_B.P$5 (5), R42.2, U3.P$2 (GND); also elsewhere on the board
GPIO30: R44.2; also elsewhere on the board
GPIO31: R43.2; also elsewhere on the board
unnamed: R35.1, U3.P$5 (EN)
unnamed: R42.1, U3.P$8 (RS)
unnamed: R43.1, U3.P$1 (D)
unnamed: R44.1, U3.P$4 (R)

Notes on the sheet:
GND
PWR
CAN
ENCODER FILTERS

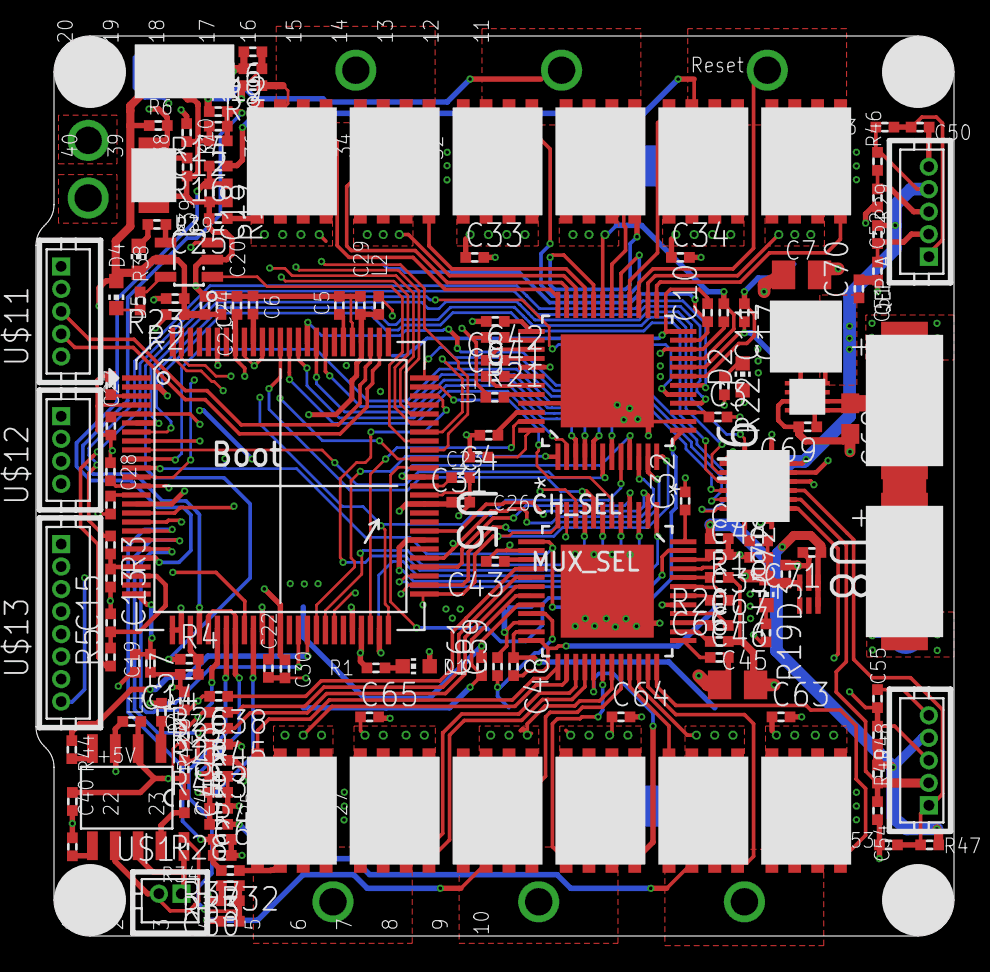
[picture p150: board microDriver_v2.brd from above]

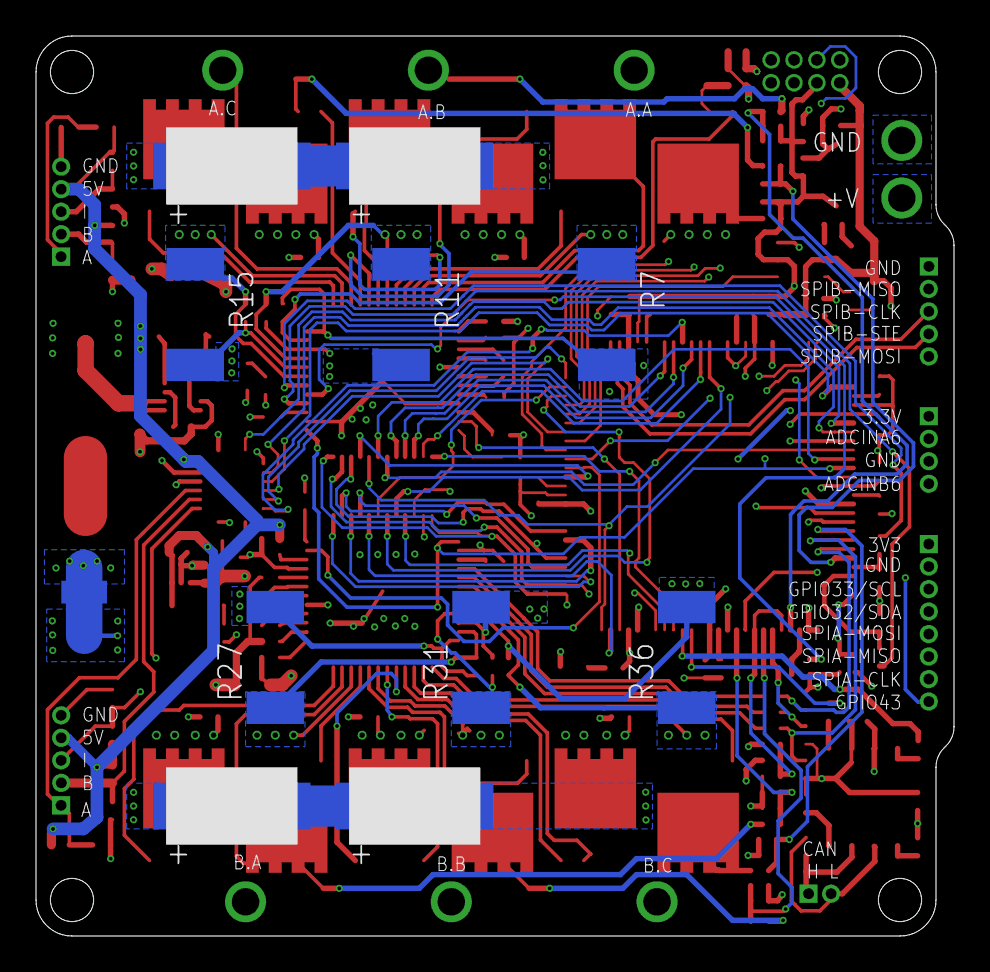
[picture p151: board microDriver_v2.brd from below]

Board: 6 copper layers, 51.0 x 50.0 mm, 172 parts (11 on the bottom side), 149 nets.

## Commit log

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2019-09-03 Update actuator module documentation
    [fastener_fhs_m3_10.STL, fastener_fhs_m3_16_plastic.STL, fastener_fhs_m3_5.STL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]
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2019-09-11 Updating 2dof leg documentation
    [foot_structure.STL, lower_leg_structure_fork.STL]
2019-09-11 Updating documentation - foot contact switch
    [foot_structure.STL, lower_leg_structure_fork.STL]
2019-09-12 Updating documentation - details actuator module
    [foot_structure.STL, lower_leg_structure_fork.STL]
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2019-09-30 Updating foot contact switch documentation
    [bom_foot_contact_switch_v1.xlsx, foot_contact_switch_v1.brd, foot_contact_switch_v1.sch]
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2019-10-02 Uploading belt tensioner rollers different diameters
    [transmission_belt_tensioner_roller.STL, transmission_belt_tensioner_roller_10.5mm.STL, transmission_belt_tensioner_roller_10mm.STL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]
2019-10-02 Uploading tool for output pulley
    [tool_output_pulley_modification.STL]
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2019-10-08 Updating foot contact switch details
    [foot_structure.STL, lower_leg_structure_fork.STL]
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2019-10-23 Adding detail pages - motor shaft and output pulley preparation
    [encoder_codewheel_kit_mount.STL]
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2019-12-09 Adding documentation - simple lower leg
    [lower_leg_solid.STL]
2019-12-13 Updating Micro Driver Documentation
    [microDriver_v2.brd, microDriver_v2.sch]
2020-02-12 Uploading step files - machined parts
    [motor_antigravity_4004_custom_shaft.STEP, transmission_pulley_at3_t10_center.STEP, transmission_pulley_at3_t10_motor.STEP]
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2020-04-27 Starting 12dof quadruped documentation
    [body_structure_back.STL, body_structure_bottom.STL, body_structure_center.STL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]
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2020-04-28 Uploading simplified Solo12 model for visualization
    [solo12_hip_fe_fl.stl, solo12_hip_fe_fr.stl, solo12_hip_fe_hl.stl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]
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2020-05-04 Starting FingerEdu and TriFingerEdu documentation
    [base_back.STL, base_front.STL, base_side_left.STL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]
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2020-05-12 Uploading Hip AA Support Step File
    [hip_aa_support.STEP]
2020-05-12 Uploading missing STL files
    [hip_adapter.STL, lower_leg_solid.STL, upper_leg_shell_cover.STL]
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2020-06-26 Updating biped robot documentation
    [body_structure_biped_back.STL, body_structure_biped_bottom.STL, body_structure_biped_front.STL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]
2020-06-26 Updating documentation - biped leg
    [hip_aa_structure_left_side_base.STL, hip_aa_structure_left_side_cover.STL, hip_aa_structure_right_side_base.STL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]
2020-06-30 added stand_attachment FreeCAD model
    - not perfect reproduction of STL, some fillets are 0.5 instead of 1 mm
    [stand_attachment.FCStd]
2020-07-02 Added FreeCAD CAD project files
    - body_structure_biped_right_side
    - micro_driver_stack_spacer
    Removed STL from stand_attachment
    [body_structure_biped_right_side.FCStd, micro_driver_stack_spacer.FCStd, stand_attachment.FCStd]
2020-07-06 Reinforcing electronics mount
    [body_structure_biped_bottom.STL]
2020-07-09 Updating documentation - leg test stand
    [adjustment_sleeve.STL, ati_sensor_bottom_plate.STL, ati_sensor_top_plate.STL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]
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2020-07-24 Adding STL file - finger adapter
    [finger_adapter.STL]
2020-07-28 added body_structure_biped_front freecad file
    [body_structure_biped_front.FCStd]
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2020-08-03 Starting documentation - nyu finger
    [actuator_module_shell_cover.STL, finger_adapter.STL, hip_aa_module_shell_base.STL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]
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2020-08-12 Moving shell stl files to 2dof leg
    [actuator_module_shell_cover.STL]
2020-08-12 Updating documentation - motor preparation
    [tool_center_pulley_assembly.STL, tool_center_pulley_protection.STL, tool_code_wheel_bonding.STL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]
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2020-09-21 Fixing view setting cad model
2020-09-30 Updating documentation - foot contact switch eagle and gerber files
    [foot_contact_switch_v1.brd, foot_contact_switch_v1.sch]
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2020-10-15 Updating 8dof quadruped v2 documentation
    [lower_leg_solid_v1.STL]
2020-10-16 Uploading wire edm drawings
    [pulley_at3_t10_wire_edm.DXF]
2020-10-16 Replacing dxf file with zip file
    [pulley_at3_t10_wire_edm.DXF]
2020-10-19 Uploading vicon top structure quadruped 8dof v2
    [body_structure_top_vicon.STL]
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2020-10-28 Correcting error in upper leg shell cover
    [actuator_module_shell_cover.STEP, hip_module_shell_cover.STL, upper_leg_module_shell_cover.STL]
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2020-12-02 Update README.md
    Fixing a broken link to the Transmission Belt Tensioner Roller.
2020-12-11 Fixing broken links to stl parts
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2021-01-22 Adding STL file body structure bottom Rev A
    [body_structure_bottom_rev_a.STL]
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2021-02-09 added input voltage for motor board
    please check if the added description is correct
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2021-02-11 Updating biped body structure top - adding STL files with IMU attachment
    [body_structure_biped_top.STL, body_structure_biped_top_imu.STL, body_structure_biped_top_imu_vicon.STL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]
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2021-03-18 Adding roll bar to quadruped 8dof v2 body structure top
    [body_structure_top_roll_bar.STL]
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2021-03-26 Starting Quadruped 12dof v1.1 documentation - autonomy upgrade
    [body_structure_center_payload.STL, body_structure_front_batterie.STL, body_structure_front_batterie_lid.STL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]
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2021-05-20 Updating Quadruped 12dof - Hip AA Support Rev A
    The height of the internal wire passage was increased - from 4mm to 7mm.
    [body_structure_hip_aa_support_rev_a.STL]
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2021-08-23 Adding Alternative Version - Hip FE Module Shell Base
    [hip_fe_module_shell_base_alt_a.STL]
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2021-09-10 Updating documentation - earlier warning - don't shorten hip aa motor phase wires
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2022-03-07 Adding STL file - tool output pulley modification
    [tool_output_pulley_modification.STL]
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2022-08-17 Uploading inertia documentation and simplified STL files for the quadruped robot 8dof v2
    [lower_leg_v2_left_side.STL, lower_leg_v2_right_side.STL, solo8_v2_body.STL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]
